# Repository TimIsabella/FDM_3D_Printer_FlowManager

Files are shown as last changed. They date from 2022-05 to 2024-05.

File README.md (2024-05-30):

# FDM 3D Printer Flow Manager

Possibly the biggest issue in FDM 3D printing is flow control, and the reasons for this are as follows:
- Inconsistent filament diameter
- Improperly calibrated flow rate
- Extruder skipping

Any one of these can cause bad prints or failed prints, which is both costly in material and time.

Flow Manager is an attempt to control all three of these critical parameters, and in addition will yield 
consistent layers which means better looking and better performing prints.

## How?
By measuring the filament diameter as it is fed, an exact flow rate can be calculated to ensure
a consistent flow. Flow Manager measures this filament diameter by two points offset around
the circumference of the filament (offset as a triangle), and averaging those points with a 
precision of up to 6 digits beyond the decimal, which results in a measurement sensitivity 
as low as 0.000001mm (1 nanometer), and a filament diameter as small as 1mm.

This measurement is achieved by amplifying the minute movements by way of dual single levers set with
high fulcrum points, and small magnets inlaid at their ends. These magnets are positioned over
highly sensitive linear hall effect sensors which measure distance by magnetic Gauss intensity. 
The length of the levers dictate the precision (longer = more precise), while canting the lever wheels at 
opposing angles ensures accuracy by simultaneously measuring at two separate points, which also negates the 
oval circumference shape which is common with filament.

In addition to diameter measurement, a digital encoder wheel can be placed as a third point of
contact separate from the lever wheels, to precisely measure overall filament movement, including retracts,
priming, skipping, jamming, and run-out.

This measurement is then sent by serial to the ESP8266 module that contains a small webserver that wirelessly
transmits g-code commands to any WiFi enabled 3D printer, continuously adjusting the flow rate live. 

Theoretically, with the precise inclusion of the encoder wheel combined with diameter measurements, the exact
length to the nozzle tip can be offset with near perfect extrusion precision, making literally any FDM 3D printer
capable of detailed prints previously unheard of while also eliminating failures.

## Current Development
Development for this project ceased in early 2020. Although the diameter measurement function
performed far better than I ever anticipated, I ran into difficulty with proprietary communication
methods for different printer manufacturers, therefore this project would probably be best suited on a
Raspberry PI board and connected to the OctoPrint platform, but would limit its use to only higher 
end printers.

Moreover, it may be possible to source a linear hall effect sensor that runs on 3v which can be connected
directly to the two I/O ports of the ESP8266, and the board flashed with all code necessary using MicroPython,
which would eliminate the need for the Nano board alltogether and vastly simplify the entire unit.

There are also many other boards in the ESP family with more functionality, more I/O pins, and possibly
that run at 5v, therefore the IC that can be used in this project is completely interchangeable.

## Parts List
- Printed model (see repo .STL files, or .MQO for Metasequoia), 0.4mm nozzle or smaller, shell is best printed upright.
- Arduino Nano (5v)
- 2x 11mm X 7mm X 3mm ball bearings
- 2x 8mm X 14mm X 4mm ball bearings
- 1x HK0306 drawn cup needle bearing, 3mm bore, 6.5mm OD, 6mm width
- 1x 5mm x 35mm dowel pin
- 2x 0.5mm X 3mm X 10mm compression springs
- 2x 4mm X 2mm round magnets
- 2x A1302 Continuous-Time Ratiometric Linear Hall-Effect Sensors (5v)
- Assorted resistors and wires set
- 1x ESP8266 ESP-01 Module. You will also need a flash tool and flash module to program the ESP8266 (there is lots of documentation online). CAUTION: the ESP8266 module is 3.6v max, so do not connect to the 5v pin on the Arduino Nano or you will destroy the ESP8266. The Arduino Nano does however have a pin for 3.3v, which powers the ESP8266 just fine.

- OPTIONAL: KY-040 Rotary Encoder Module (untested). This is what I was going to use to measure the filament movement,
although it was never implemented. Essentially this encoder would be attached to a wheel that rotates with the
movement of the filament, and calculated along with measurement.

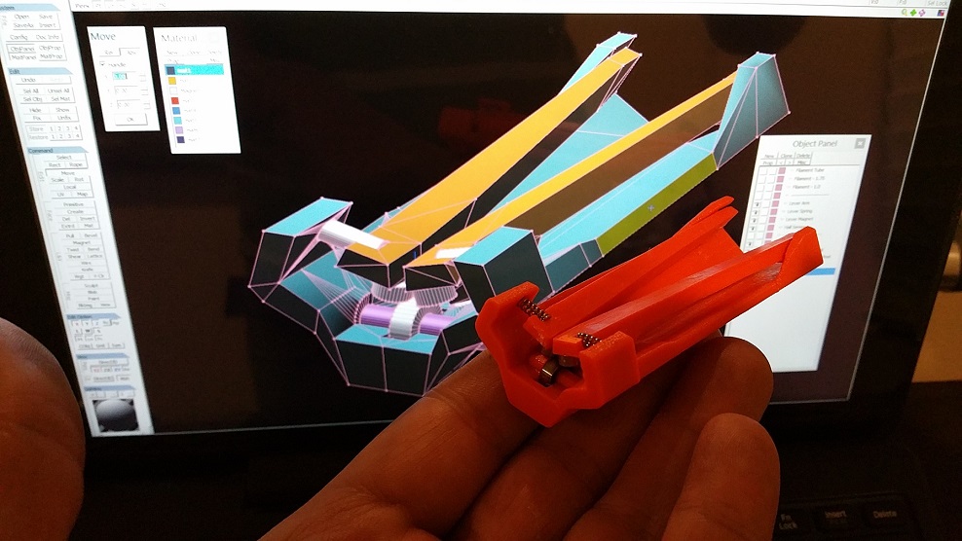
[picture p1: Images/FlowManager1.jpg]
FlowManager1

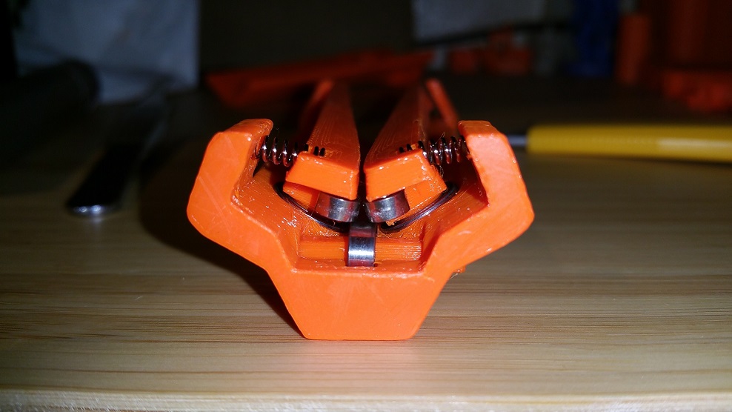
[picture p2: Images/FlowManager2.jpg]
FlowManager2

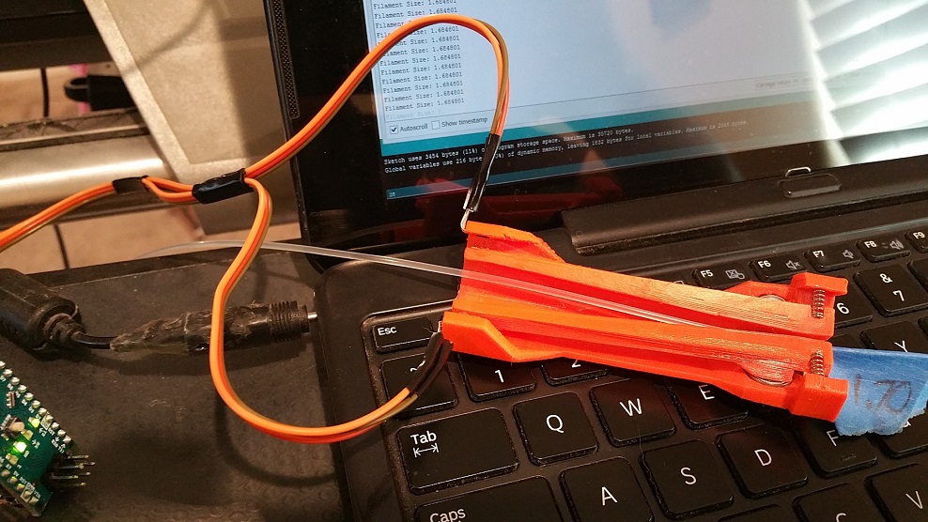
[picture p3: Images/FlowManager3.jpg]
FlowManager3

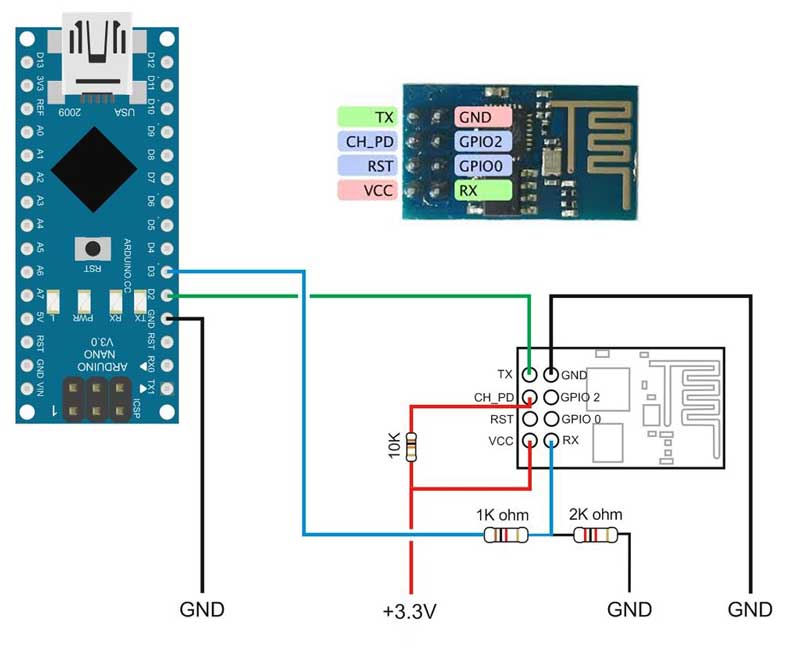
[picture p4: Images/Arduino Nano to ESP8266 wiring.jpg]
Wiring


## Screenshots from Version 11 (see .MQO file for Metasequoia)
- [Download Metasequoia](https://www.metaseq.net/en)

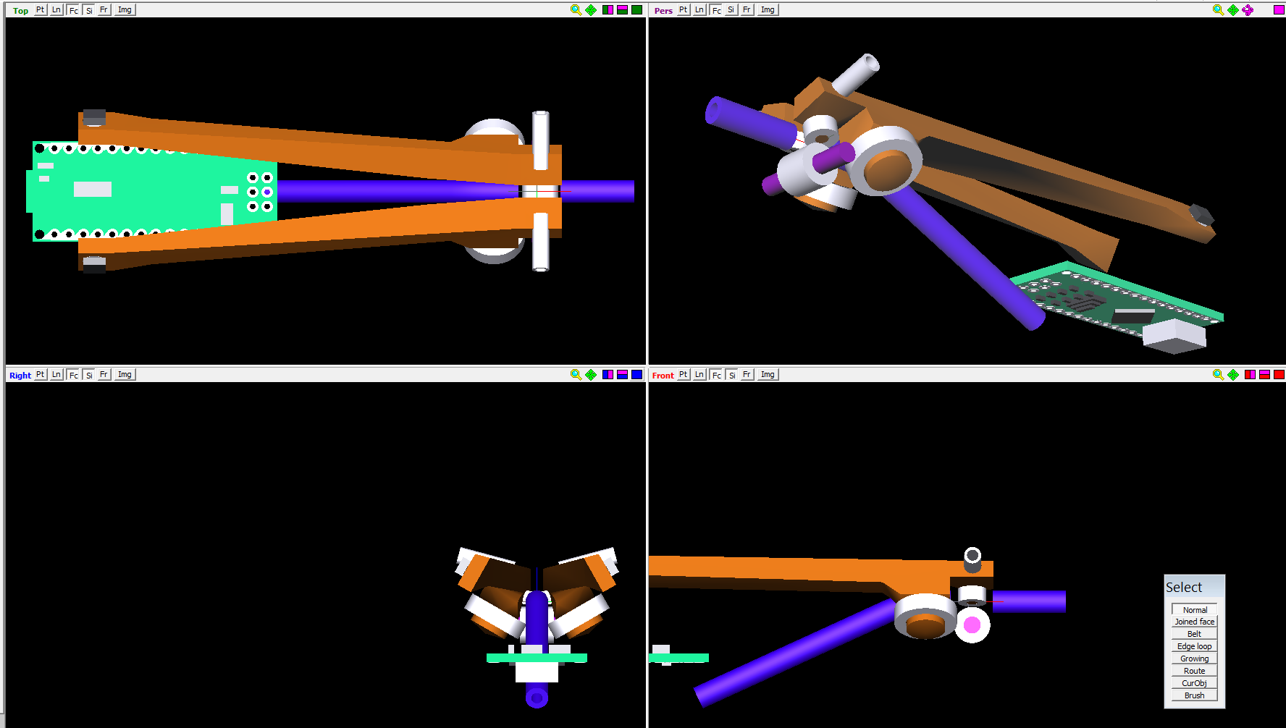
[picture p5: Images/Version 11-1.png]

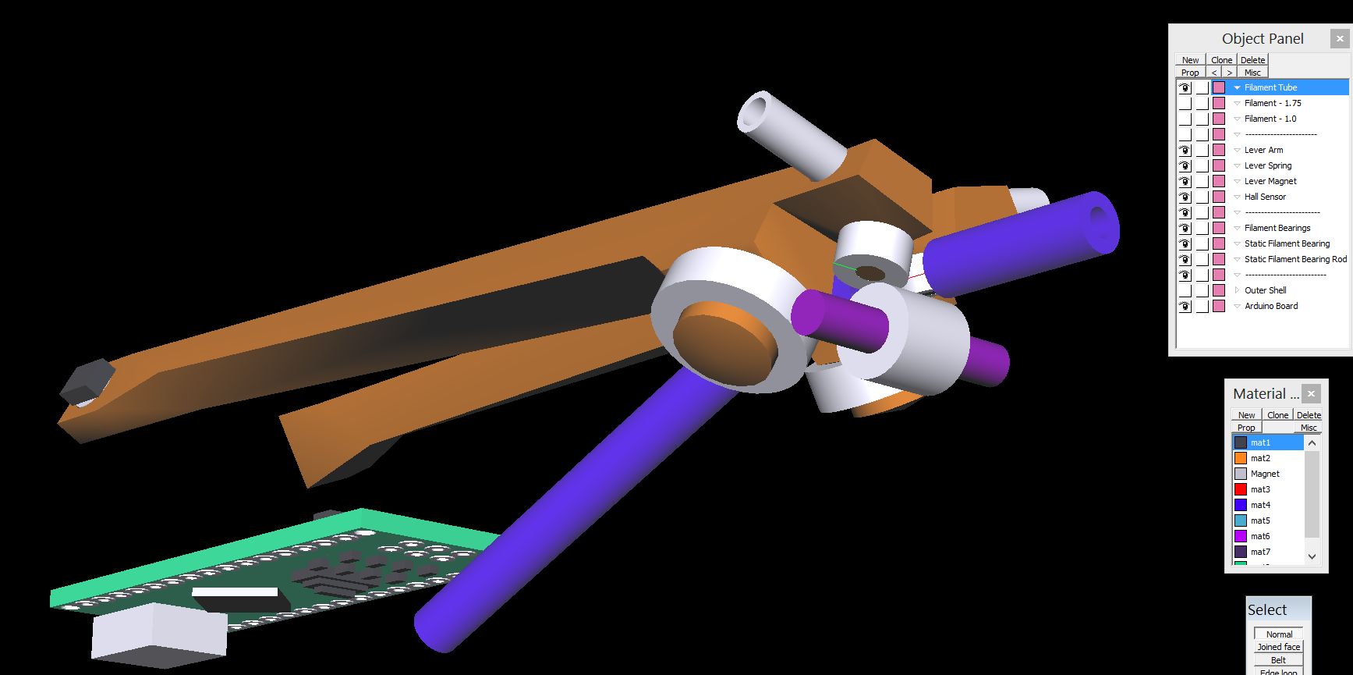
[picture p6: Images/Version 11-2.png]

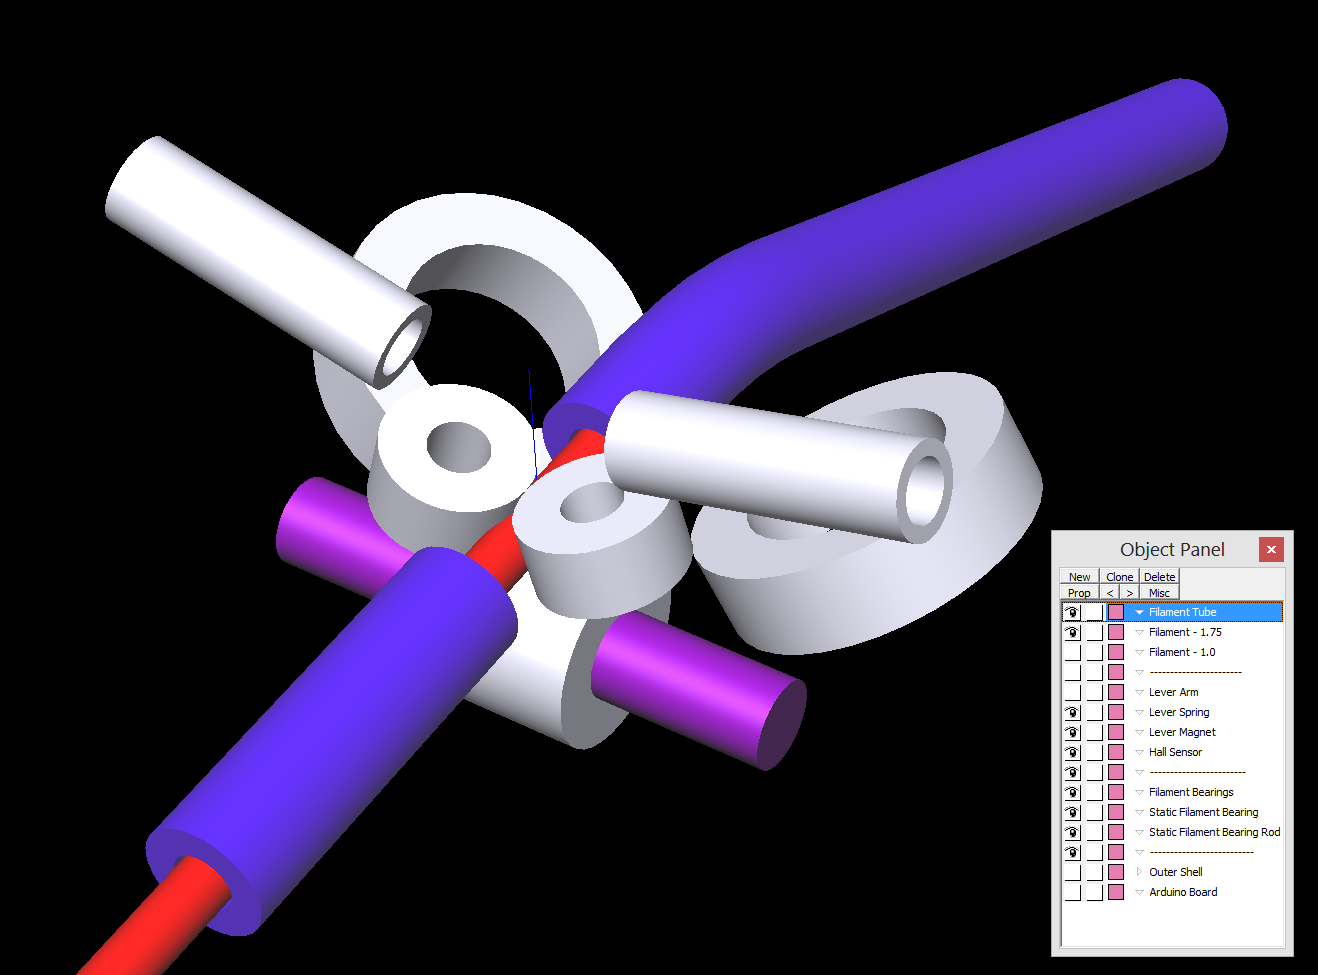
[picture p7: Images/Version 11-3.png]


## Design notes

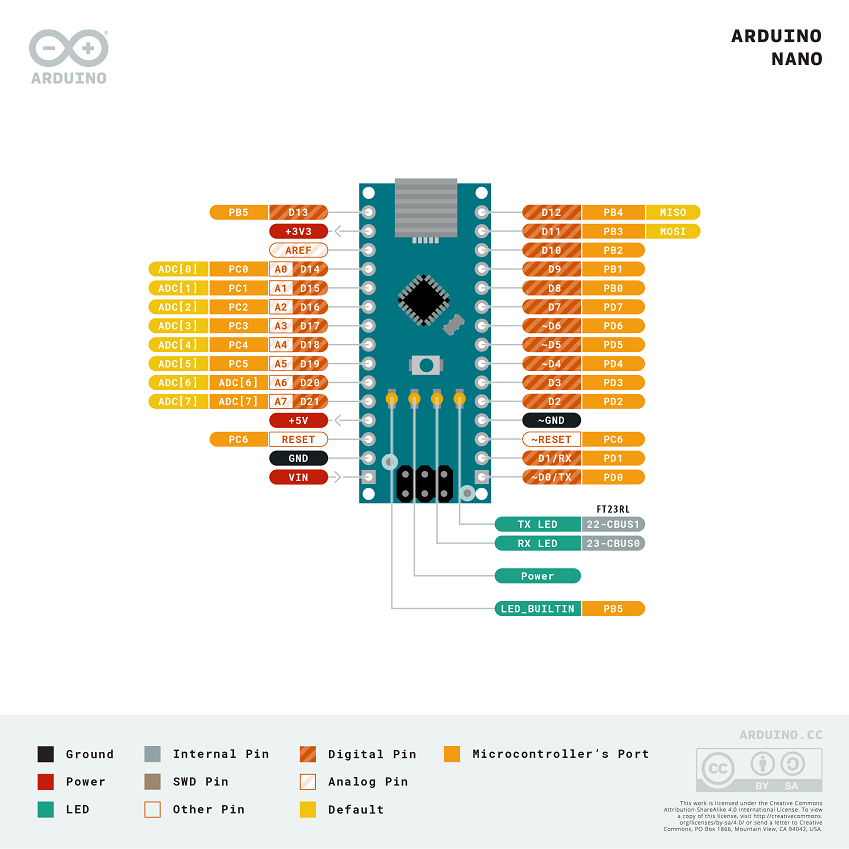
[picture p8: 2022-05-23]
Images/Arduino Nano Pinout.png

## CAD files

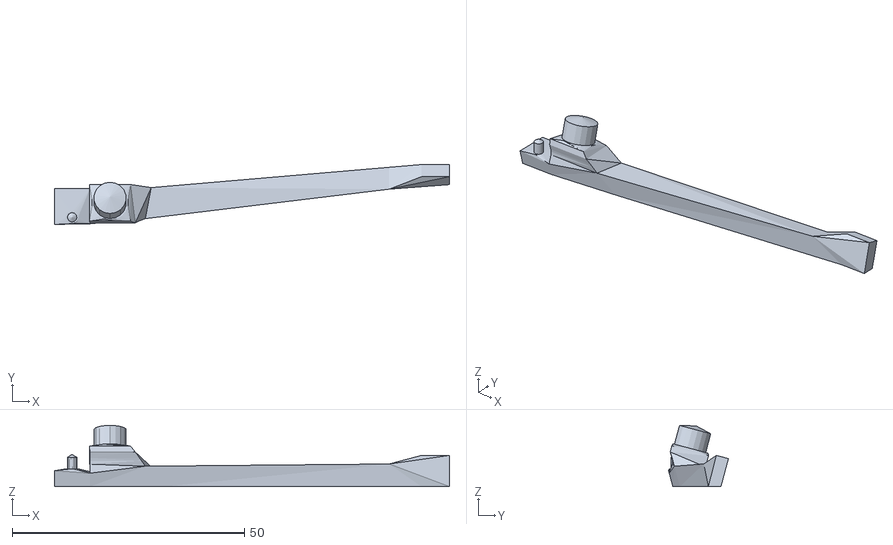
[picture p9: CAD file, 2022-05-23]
3D Models/FlowManager - Left Lever.stl
85.0 x 12.9 x 13.2

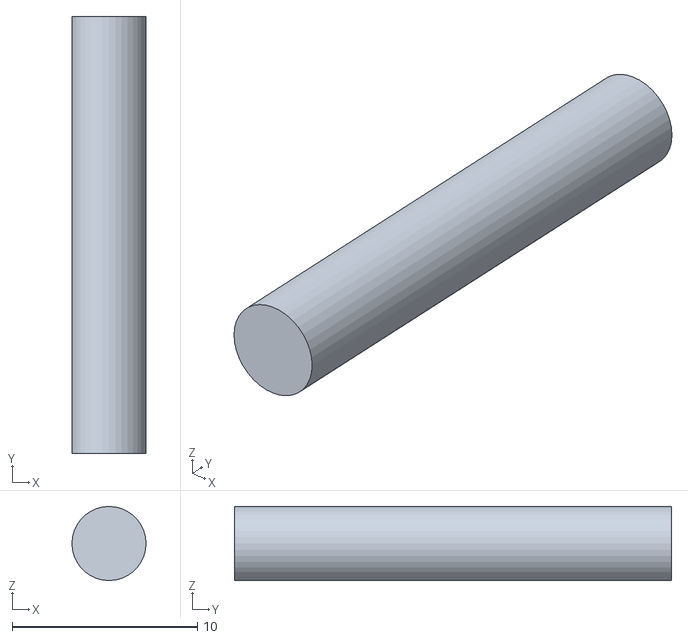
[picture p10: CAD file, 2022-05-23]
3D Models/FlowManager - Bearing Rod.stl
4.00 x 23.6 x 4.00

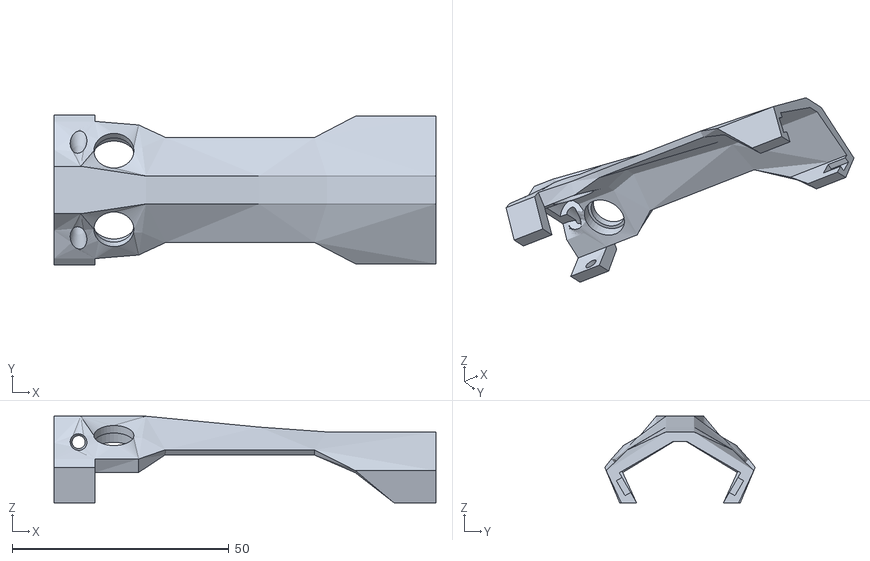
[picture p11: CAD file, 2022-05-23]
3D Models/FlowManager - Shell.stl
88.2 x 34.7 x 20.0

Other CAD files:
3D Models/FlowManager - Right Lever.stl

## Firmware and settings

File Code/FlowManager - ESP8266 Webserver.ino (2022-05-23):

#include <ESP8266WiFi.h>
#include <ESP8266WebServer.h>
#include <ESP8266WiFiMulti.h> 
#include <WiFiClient.h>
#include <ESP8266HTTPClient.h>

ESP8266WiFiMulti WifiMultiW;      //Create an instance of the ESP8266WiFiMulti class, called 'wifiMulti'
ESP8266WebServer ServerS(80);     //Create a webserver object that listens for HTTP request on port 80
WiFiClient client;                //Initialize the client library

String HTMLindex;
String HTTPsendStr;
String HTTPresponseStr;
String PrinterURL = "http://192.168.8.124";
int PrinterPort = 80;
int NewDataRdy = 0;

//Serial Read
String ESPreadStr;
char ESPreadChar[32];

//Float Parsing For 6 Digits of Acccuracy
float ESPreadNum;
String FloatFrontStr;
float FloatFrontF;
String FloatEndStr;
float FloatEndF;

//Function HTTP handlers
void handleRoot();
void handleNotFound();

//Misc variables
int A;
int B;
int C;

///////////Setup///////////
void setup(void)
     {
      //Establish serial settings
      //Serial.begin(115200);
      Serial.begin(34000);
      Serial.print("RX TX Serial Established at 34000...");
      Serial.setTimeout(500);
      Serial.println('\n');
      delay(10);

      //Add access point
      WifiMultiW.addAP("WiFiRouterSSID", "Password");  //Add Wi-Fi network
      
      Serial.println("Connecting ...");
      while(WifiMultiW.run() != WL_CONNECTED) //Wait for Wi-Fi connect
           {
            delay(250);
            Serial.print('.');
           }

      //Print connection status
      Serial.println('\n');
      Serial.print("Connected to ");
      Serial.println(WiFi.SSID());              //Print connected network SSID
      Serial.print("IP address:\t");
      Serial.println(WiFi.localIP());           //Print IP address of ESP8266
      
      ServerS.on("/", handleRoot);              //Client requests handleRoot function URI "/"
      ServerS.onNotFound(handleNotFound);       //Client requests unknown URI
      
      ServerS.begin();                          //Start the server

      WiFiClient client;
     }

///////////Loop///////////
void loop(void)
     {
      RecieveDataV();
      ServerS.handleClient();
     }
    
///////////Parse Serial data into float///////////
void RecieveDataV()
     {
      if(NewDataRdy)
        {
         if(Serial.available() && (Serial.read() == '\a'))
           {
            ESPreadStr = Serial.readStringUntil('\n');
            A = ESPreadStr.length();
            
            //Capture BEFORE decimal and convert to int with float
            FloatFrontStr = Serial.readStringUntil('.');
            B = FloatFrontStr.length();
            FloatFrontStr = ESPreadStr.substring(0, (B-1));
            FloatFrontF = 0.0000001 + FloatFrontStr.toInt();
            
            //Capture AFTER decimal and convert to int with float
            FloatEndStr = ESPreadStr.substring(B, A); //Six digits
            FloatEndF = 0.0000001 + FloatEndStr.toInt(); 
            for(int ZZ = 0; ZZ <= 5; ZZ++) {FloatEndF = FloatEndF / 10;} //Move decimal over six places
            
            //Combine to create float
            ESPreadNum = FloatFrontF + FloatEndF;

            NewDataRdy = 0;
           }
        }
     }

///////////Output Webpage///////////
void handleRoot() 
     {
      HTMLindex  += "<html><head><title>Filament Flow Manager</title></head>";
      HTMLindex  += "<body>";
      
      HTMLindex  += "<h1>Filament Flow Manager</h1>";
      HTMLindex  += "<BR>";
      
      HTMLindex  += "<h2>";
      HTMLindex  += "Measured Filament Size: ";
      HTMLindex  += String(ESPreadNum, 6);
      HTMLindex  += "<BR>";
      HTMLindex  += "<BR>";
      
      HTMLindex  += "<h3>";
      HTMLindex  += "H3 text";
      HTMLindex  += "</h3>";
      HTMLindex  += "<BR>";
      
      HTMLindex  += "<h4>";
      HTMLindex  += "<p1>Input text below</p>";
      HTMLindex  += "<textarea name=\"TextBox1\" cols=\"50\" rows=\"5\">This is a textbox</textarea>";
      HTMLindex  += "</h4>";
      HTMLindex  += "<BR>";
      
      HTMLindex  += "<h5>";
      HTMLindex  += "<form action=\"/get\"> input1: <input type=\"text\" name=\"input1\">";
      HTMLindex  += "<input type=\"submit\" value=\"Submit\">";
      HTMLindex  += "</form>";
      HTMLindex  += "</h5>";
      HTMLindex  += "<BR><BR>";
      
      HTTPClient http;
      HTTPsendStr = "http://192.168.8.124/set?code=G28";
      http.begin(HTTPsendStr);
      //http.addHeader("Content-Type", "text/plain");
      HTTPresponseStr = http.GET();
      http.end();
      
      HTMLindex  += "PRINTER SEND STRING: ";
      HTMLindex  += HTTPsendStr;
      HTMLindex  += "<BR><BR>";
      HTMLindex  += "PRINTER RESPONSE: ";
      HTMLindex  += HTTPresponseStr;
      
      HTMLindex  += "<BR><BR><BR>";
      
      C++; //Page views
      HTMLindex  += "Page Views: ";
      HTMLindex  += C;
      
      //Send webpage
      ServerS.send(200, "text/html", HTMLindex);   //Http status 200 (Ok)
      
      HTMLindex = "";
      NewDataRdy = 1;
     }

//Ouput Webpage 404 error
void handleNotFound()
    {
     ServerS.send(404, "text/plain", "404: Not found");
    }


/////////////////////////////////Debug stuff/////////////////////////////////

/*
      HTMLindex  += "ESPreadStr: ";       
      HTMLindex  += ESPreadStr;
      HTMLindex  += "<BR>";
      HTMLindex  += "FloatFrontStr: ";
      HTMLindex  += FloatFrontStr;
      HTMLindex  += "<BR>";
      HTMLindex  += "FloatFrontF: ";       
      HTMLindex  += String(FloatFrontF, 6);
      HTMLindex  += "<BR>";
      HTMLindex  += "FloatEndStr: ";
      HTMLindex  += FloatEndStr;
      HTMLindex  += "<BR>";
      HTMLindex  += "FloatEndF: ";
      HTMLindex  += String(FloatEndF, 6);
      HTMLindex  += "</h2>";
      HTMLindex  += "<BR>";
*/

/*
      HTMLindex  += "CONNECTION STATUS: ";       
      //Connect to printer if not already
      if(!client.connected()) client.connect(PrinterURL, PrinterPort);
      
      if(client.connected()) 
        {
         HTMLindex += "!CONNECTED TO PRINTER!";
         client.println("/set?code=G28");
        }
      
      if(!client.connected())
        {
         HTMLindex += "Not connected to printer";
        }
*/

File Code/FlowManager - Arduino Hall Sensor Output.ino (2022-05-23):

#include <SoftwareSerial.h>

//Constants
float Tuning = 568.5;
float FilamentSize = 1.75;

//Analog pins
float AnalogPin0;
float AnalogPin1;

//Variables
float AnalogAvg;
float FilamentCalc;
float FilamentPercent;

//Serial Transmit Pin
////Recieve = pin 0
////Transmit = pin 1
SoftwareSerial NANOserial(1,2);

//SETUP
void setup()
{
Serial.begin(34000);
//Serial.print("RX TX Serial Established at 34000...");
//Serial.println();
}

//MAIN LOOP
void loop()
{
//Calculate Filament Size
AnalogPin0 = analogRead(0);
AnalogPin1 = analogRead(1);
AnalogAvg = (AnalogPin0 + AnalogPin1) / 2;
FilamentCalc = (FilamentSize / AnalogAvg) * Tuning;
FilamentPercent = (FilamentSize / FilamentCalc) * 100;

//Print to Serial
Serial.print("\a");               //Begin marker
Serial.print(FilamentPercent, 6); //6 decimal places
Serial.println();

delay(500); 
}

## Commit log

2022-05-23 Create Arduino Hall Sensor Output.ino
2022-05-23 Create FlowManager ESP8266 Webserver.ino
2022-05-26 Rename Arduino Hall Sensor Output.ino to FlowManager - Arduino Hall Sensor Output.ino
2022-05-26 Rename FlowManager ESP8266 Webserver.ino to FlowManager - ESP8266 Webserver.ino
2024-05-06 Added dowel pin
